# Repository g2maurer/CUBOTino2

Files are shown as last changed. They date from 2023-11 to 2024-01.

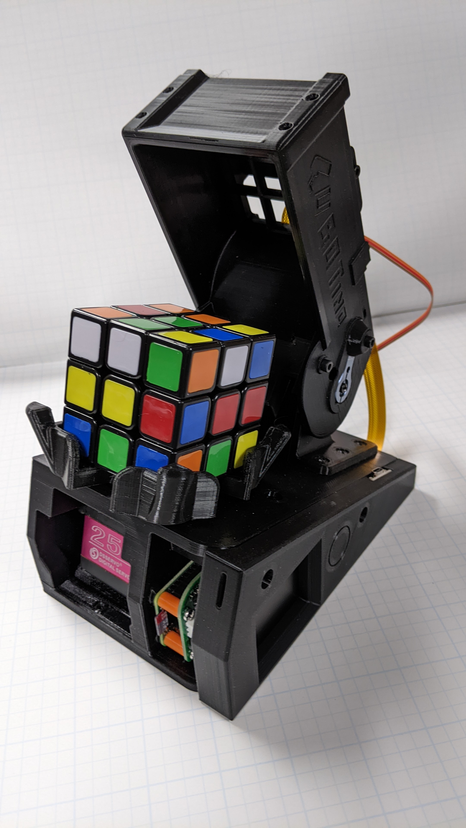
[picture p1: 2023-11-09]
Images/CUBOTino.jpg

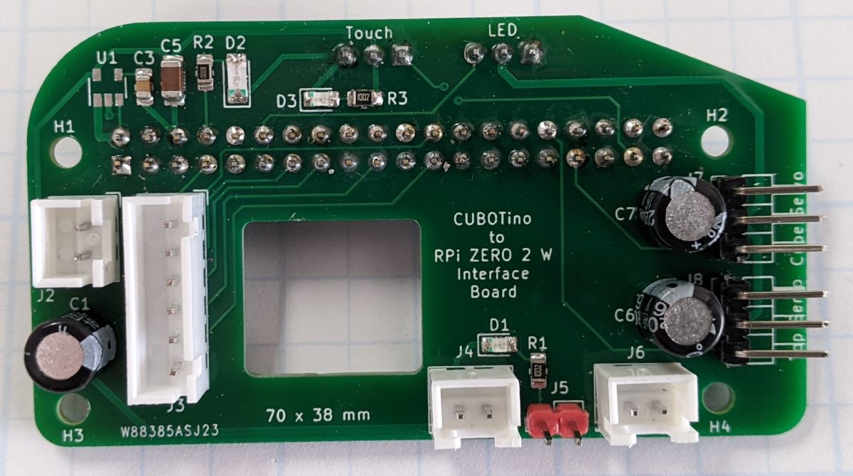
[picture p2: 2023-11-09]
Images/Cubotino_Interface_board_lr.jpg

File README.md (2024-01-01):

# CUBOTino2
 CUBOTino Modifications:
 1. No changes were made to software.
 2. Designed PCB (shield) to connect with RPi board.
 3. Modified cover STL file to be able to mount Display.
 4. Display is now cabled to PCB, not directly attached.
 5. Added photos in Images to help explain board connections and Display mounting.
 6. Photo DisplayMountScrews provides the part number for the screws used to mount the display. Screws were purchased from McMaster-Carr.
 7. The Bill of Materials (BOM) in found in the file PCB/CUBOTino2.csv
 8. The schematic is in the file PCB/CUBOTino2.pdf
 9. See file PCB/SMD Parts.txt for part sourcing info.

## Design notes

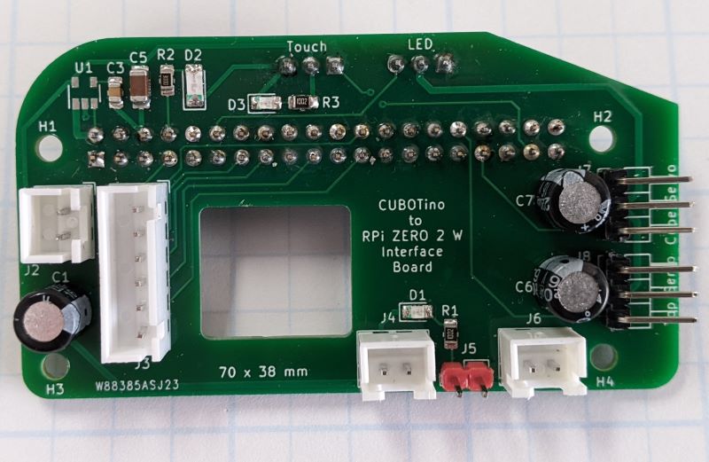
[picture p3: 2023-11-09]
Images/CUBOTino_5x7a.jpg

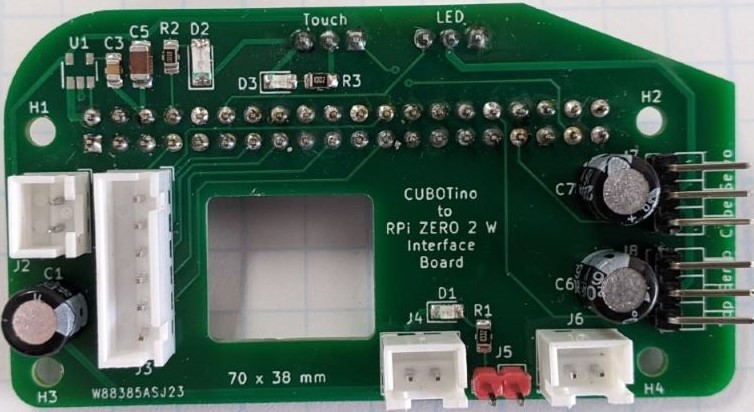
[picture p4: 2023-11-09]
Images/Cubotino_Interface_board_800.jpg

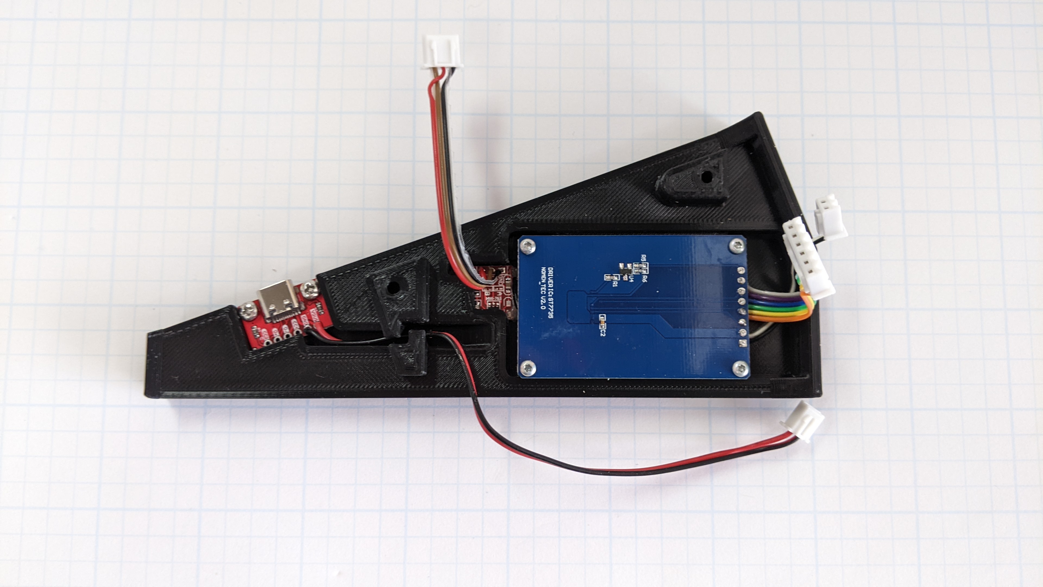
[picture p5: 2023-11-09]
Images/Display.jpg

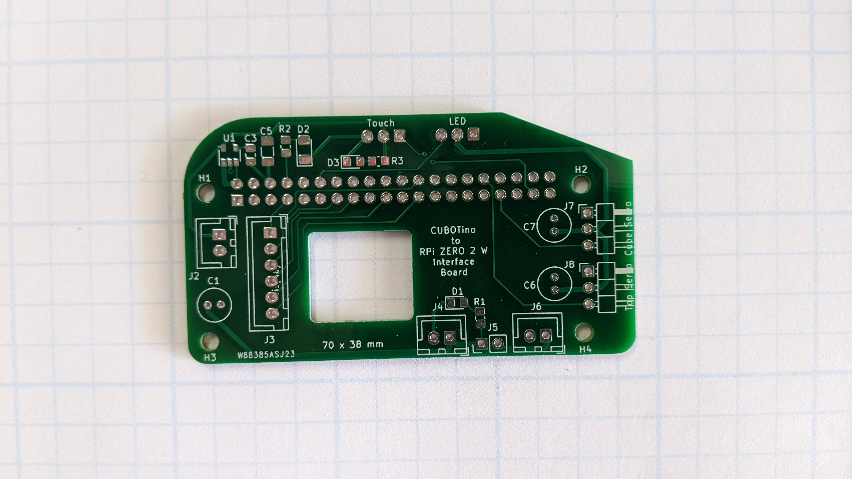
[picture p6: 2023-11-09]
Images/PCB.jpg

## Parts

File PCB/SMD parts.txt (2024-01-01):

I purchased the resistors, capacitors and LEDs on Amazon. They come as
> assorted kits. Here are some Amazon links to what I purchased:
>
> Resistors:
> https://www.amazon.com/gp/product/B09538ZBCR/ref=ppx_yo_dt_b_search_asin_title?ie=UTF8&th=1
> Capacitors:
> https://www.amazon.com/gp/product/B06XD3K15S/ref=ppx_yo_dt_b_search_asin_title?ie=UTF8&psc=1
> LEDs:
> https://www.amazon.com/gp/product/B01CUGA8JO/ref=ppx_yo_dt_b_search_asin_title?ie=UTF8&th=1
> Note: these are for is 0805 size components.
>
> The two components that are 1206 size are C5 and D2 (2.2uF capacitor and
> LED).
> Here is the links to the 1206 size components:
> LED:
> https://www.amazon.com/gp/product/B01CUGAFEC/ref=ppx_yo_dt_b_search_asin_title?ie=UTF8&th=1
> Capacitor:
> https://www.amazon.com/gp/product/B06XDHC93D/ref=ppx_yo_dt_b_search_asin_title?ie=UTF8&psc=1

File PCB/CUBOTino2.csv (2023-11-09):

Source: | C:\Users\gmaur\Documents\KiCad Projects\CUBOTino2\CUBOTino2.sch
Date: | 8/23/2023 4:29:55 PM
Tool: | Eeschema (5.1.10)-1
Component Count: | 28
Ref | Value | Footprint | Datasheet | Manufacturer | Vendor
C1 | 220uF 16V | Capacitor_THT:C_Radial_D5.0mm_H7.0mm_P2.00mm | ~
C2 | 100nF | Capacitor_SMD:C_0805_2012Metric_Pad1.18x1.45mm_HandSolder | ~
C3 | 10nF | Capacitor_SMD:C_0805_2012Metric_Pad1.18x1.45mm_HandSolder | ~
C4 | 100nF | Capacitor_SMD:C_0805_2012Metric_Pad1.18x1.45mm_HandSolder | ~
C5 | 2.2uF | Capacitor_SMD:C_1206_3216Metric_Pad1.33x1.80mm_HandSolder | ~
C6 | 220uF 16V | Capacitor_THT:C_Radial_D5.0mm_H7.0mm_P2.00mm | ~
C7 | 220uF 16V | Capacitor_THT:C_Radial_D5.0mm_H7.0mm_P2.00mm | ~
D1 | LED | LED_SMD:LED_0805_2012Metric_Pad1.15x1.40mm_HandSolder | ~
D2 | LED | LED_SMD:LED_1206_3216Metric_Pad1.42x1.75mm_HandSolder | ~
D3 | LED | LED_SMD:LED_0805_2012Metric_Pad1.15x1.40mm_HandSolder | ~
H1 | MountingHole | MountingHole:MountingHole_2.7mm | ~
H2 | MountingHole | MountingHole:MountingHole_2.7mm | ~
H3 | MountingHole | MountingHole:MountingHole_2.7mm | ~
H4 | MountingHole | MountingHole:MountingHole_2.7mm | ~
J1 | P1 | Connector_PinSocket_2.54mm:PinSocket_2x20_P2.54mm_Vertical | https://www.raspberrypi.org/documentation/hardware/raspberrypi/schematics/rpi_SCH_3bplus_1p0_reduced.pdf
J2 | TFT_PWR | Connector_JST:JST_XH_B2B-XH-A_1x02_P2.50mm_Vertical | ~
J3 | TFT | Connector_JST:JST_XH_B6B-XH-A_1x06_P2.50mm_Vertical | ~
J4 | 5V | Connector_JST:JST_XH_B2B-XH-A_1x02_P2.50mm_Vertical | ~
J5 | Jump | Connector_PinHeader_2.54mm:PinHeader_1x02_P2.54mm_Vertical | ~
J6 | 5VP | Connector_JST:JST_XH_B2B-XH-A_1x02_P2.50mm_Vertical | ~
J7 | Cube | Connector_PinHeader_2.54mm:PinHeader_1x03_P2.54mm_Horizontal | ~
J8 | Top | Connector_PinHeader_2.54mm:PinHeader_1x03_P2.54mm_Horizontal | ~
J9 | LED | Connector_JST:JST_XH_B3B-XH-A_1x03_P2.50mm_Vertical | ~
J10 | Touch | Connector_JST:JST_XH_B3B-XH-A_1x03_P2.50mm_Vertical | ~
R1 | 10k | Resistor_SMD:R_0805_2012Metric_Pad1.20x1.40mm_HandSolder | ~
R2 | 330 | Resistor_SMD:R_0805_2012Metric_Pad1.20x1.40mm_HandSolder | ~
R3 | 10k | Resistor_SMD:R_0805_2012Metric_Pad1.20x1.40mm_HandSolder | ~
U1 | LP2985-3.3 | Package_TO_SOT_SMD:SOT-23-5 | http://www.ti.com/lit/ds/symlink/lp2985.pdf

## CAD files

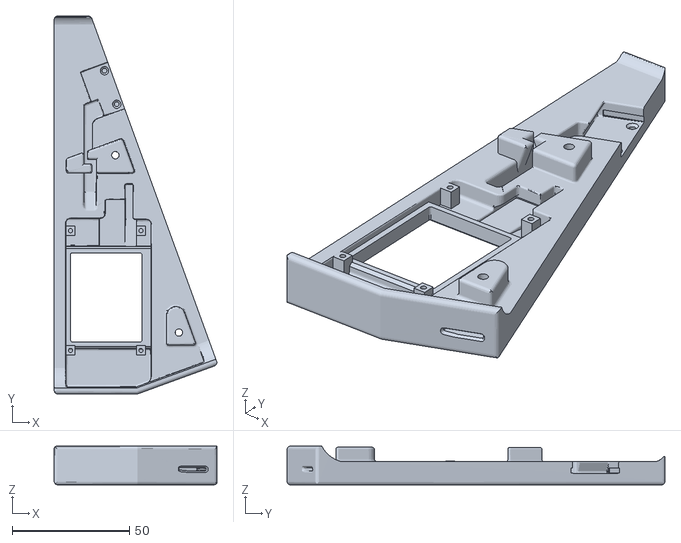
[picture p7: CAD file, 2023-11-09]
STL/PCB_Cover6.stl
69.3 x 161.0 x 16.5

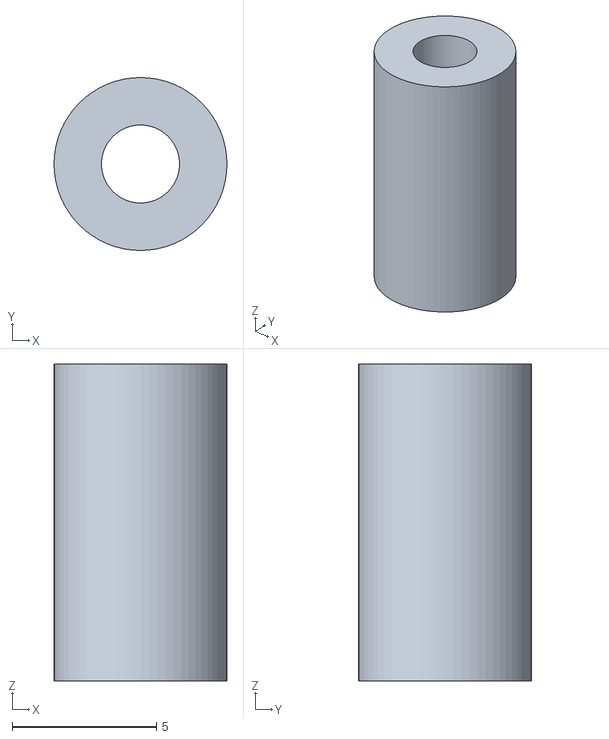
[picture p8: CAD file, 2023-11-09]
STL/Spacer_6x11mm.stl
6.00 x 6.00 x 11.0

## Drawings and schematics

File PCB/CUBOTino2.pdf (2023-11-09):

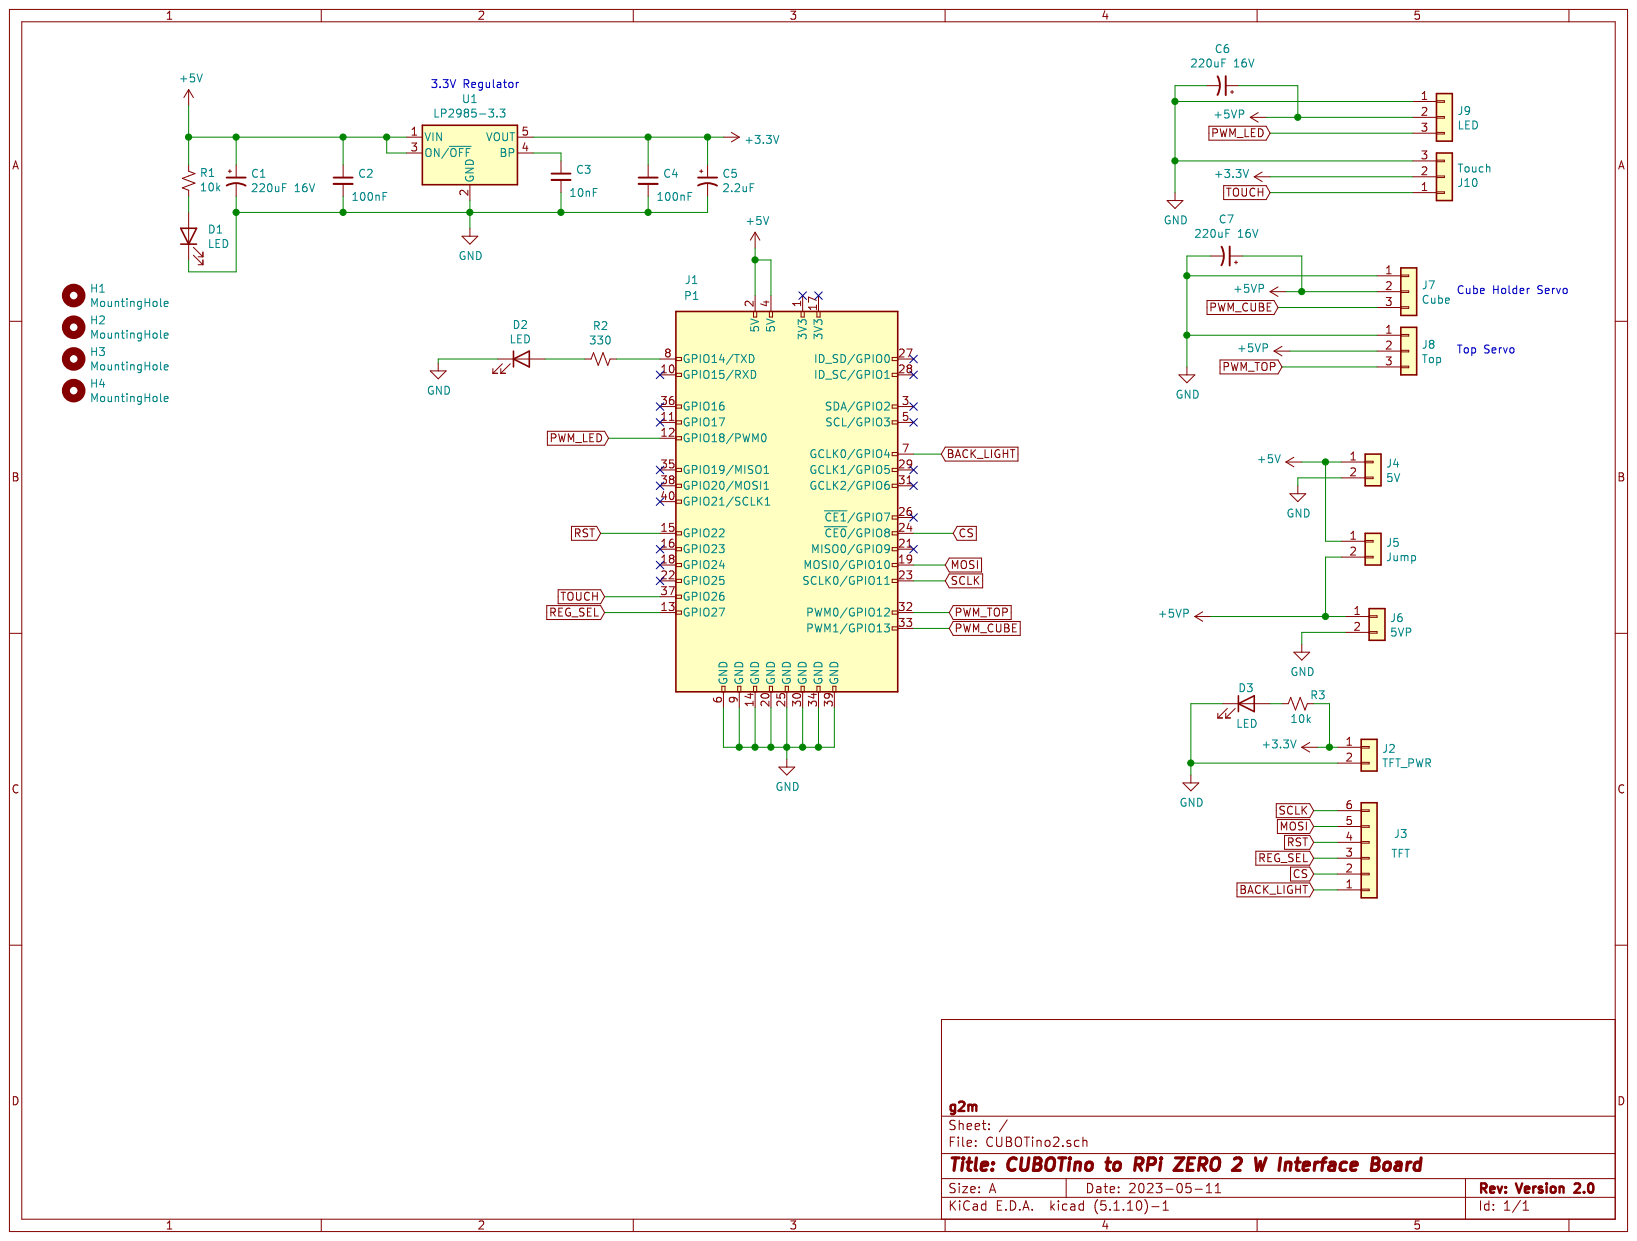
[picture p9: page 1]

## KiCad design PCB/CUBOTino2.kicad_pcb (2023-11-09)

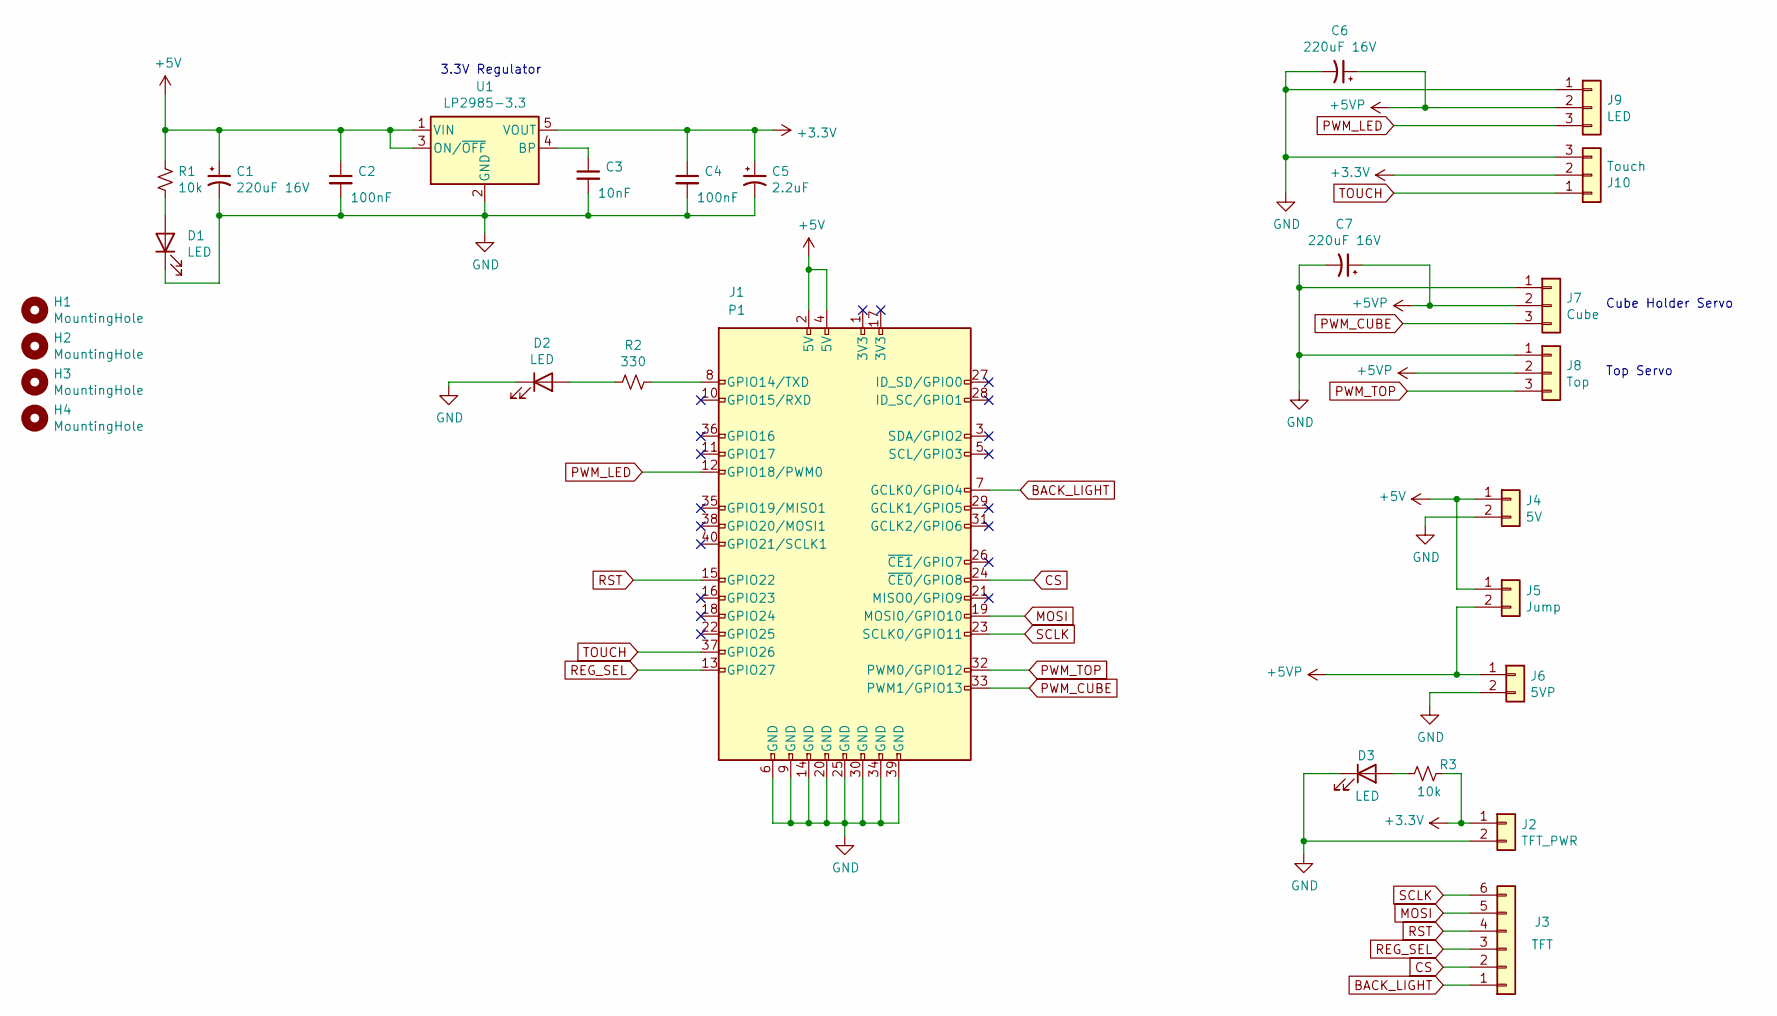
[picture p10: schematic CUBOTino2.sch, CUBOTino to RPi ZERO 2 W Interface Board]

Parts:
C1, C6, C7: 220uF 16V; C_Radial_D5.0mm_H7.0mm_P2.00mm
C2, C4: 100nF; C_0805_2012Metric_Pad1.18x1.45mm_HandSolder
C3: 10nF; C_0805_2012Metric_Pad1.18x1.45mm_HandSolder
C5: 2.2uF; C_1206_3216Metric_Pad1.33x1.80mm_HandSolder
D1, D3: LED; LED_0805_2012Metric_Pad1.15x1.40mm_HandSolder
D2: LED; LED_1206_3216Metric_Pad1.42x1.75mm_HandSolder
H1, H2, H3, H4: MountingHole; MountingHole_2.7mm
J1: P1; PinSocket_2x20_P2.54mm_Vertical
J2: TFT_PWR; JST_XH_B2B-XH-A_1x02_P2.50mm_Vertical
J3: TFT; JST_XH_B6B-XH-A_1x06_P2.50mm_Vertical
J4: 5V; JST_XH_B2B-XH-A_1x02_P2.50mm_Vertical
J5: Jump; PinHeader_1x02_P2.54mm_Vertical
J6: 5VP; JST_XH_B2B-XH-A_1x02_P2.50mm_Vertical
J7: Cube; PinHeader_1x03_P2.54mm_Horizontal
J8: Top; PinHeader_1x03_P2.54mm_Horizontal
J9: LED; JST_XH_B3B-XH-A_1x03_P2.50mm_Vertical
J10: Touch; JST_XH_B3B-XH-A_1x03_P2.50mm_Vertical
R1, R3: 10k; R_0805_2012Metric_Pad1.20x1.40mm_HandSolder
R2: 330; R_0805_2012Metric_Pad1.20x1.40mm_HandSolder
U1: LP2985-3.3; SOT-23-5

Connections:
+3V3: C4.1, C5.1, J2.1, J10.2, R3.2, U1.5 (VOUT)
+5V: C1.1, C2.1, J1.2 (5V), J1.4 (5V), J4.1, J5.1, R1.2, U1.1 (VIN), U1.3 (ON/~OFF~)
+5VP: C6.1, C7.1, J5.2, J6.1, J7.2, J8.2, J9.2
BACK_LIGHT: J1.7 (GCLK0/GPIO4), J3.1
CS: J1.24 (~CE0~/GPIO8), J3.2
GND: C1.2, C2.2, C3.2, C4.2, C5.2, C6.2, C7.2, D1.1 (K), D2.1 (K), D3.1 (K), J1.6 (GND), J1.9 (GND), J1.14 (GND), J1.20 (GND), J1.25 (GND), J1.30 (GND), J1.34 (GND), J1.39 (GND), J2.2, J4.2, J6.2, J7.1, J8.1, J9.1, J10.3, U1.2 (GND)
MOSI: J1.19 (MOSI0/GPIO10), J3.5
unnamed: C3.1, U1.4 (BP)
unnamed: D1.2 (A), R1.1
unnamed: D2.2 (A), R2.1
unnamed: D3.2 (A), R3.1
unnamed: J1.8 (GPIO14/TXD), R2.2
PWM_CUBE: J1.33 (PWM1/GPIO13), J7.3
PWM_LED: J1.12 (GPIO18/PWM0), J9.3
PWM_TOP: J1.32 (PWM0/GPIO12), J8.3
REG_SEL: J1.13 (GPIO27), J3.3
RST: J1.15 (GPIO22), J3.4
SCLK: J1.23 (SCLK0/GPIO11), J3.6
TOUCH: J1.37 (GPIO26), J10.1

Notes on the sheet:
Cube Holder Servo
Top Servo
3.3V Regulator

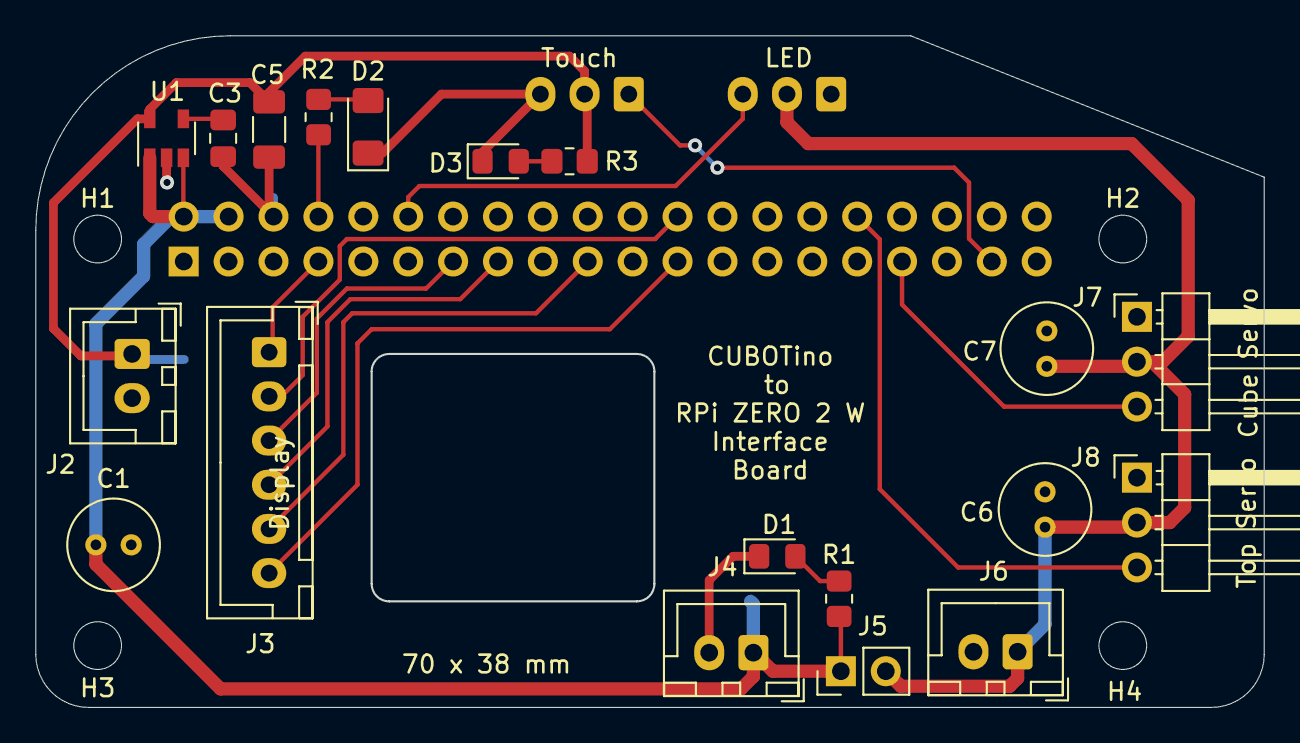
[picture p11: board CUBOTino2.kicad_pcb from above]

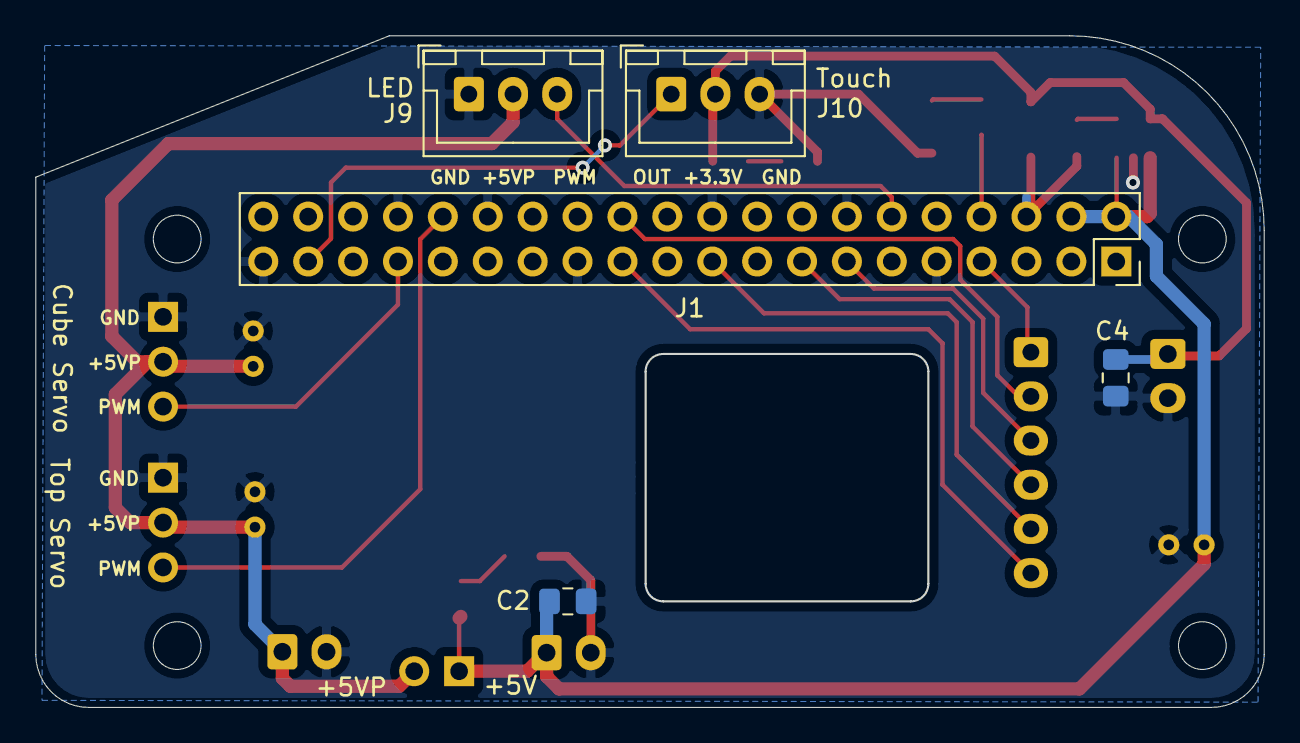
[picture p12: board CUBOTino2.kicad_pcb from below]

Board: 2 copper layers, 69.5 x 38.0 mm, 28 parts (5 on the bottom side), 19 nets.

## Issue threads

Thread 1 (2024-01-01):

SMD's

daincrawford, 2024-01-01:
I there any chance we could get a list of the LEDs, resistors and small surface mount capacitors. Adafruit has the large capacitors, but none of the surface mount. I have looked at DigiKey and Mouser, but I have no idea what I actually need. I was able to get your boards from PCBway. Thank you very much for making them available and I am really looking forward to completing this project.
I have all of the rest of the parts either ordered or already received.  Again thank you for your fine work.

g2maurer, 2024-01-01:
I will send you a list.

On Mon, Jan 1, 2024 at 6:04 AM daincrawford ***@***.***>
wrote:

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

g2maurer, 2024-01-01:
I purchased the resistors, capacitors and LEDs on Amazon. They come as assorted kits. Here are some Amazon links to what I purchased:

Resistors:  https://www.amazon.com/gp/product/B09538ZBCR/ref=ppx_yo_dt_b_search_asin_title?ie=UTF8&th=1
Capacitors:  https://www.amazon.com/gp/product/B06XD3K15S/ref=ppx_yo_dt_b_search_asin_title?ie=UTF8&psc=1
LEDs:  https://www.amazon.com/gp/product/B01CUGA8JO/ref=ppx_yo_dt_b_search_asin_title?ie=UTF8&th=1
Note: these are for is 0805 size components.

The two components that are 1206 size are C5 and D2 (2.2uF capacitor and LED).
Here is the links to the 1206 size components:
LED:  https://www.amazon.com/gp/product/B01CUGAFEC/ref=ppx_yo_dt_b_search_asin_title?ie=UTF8&th=1
Capacitor:  https://www.amazon.com/gp/product/B06XDHC93D/ref=ppx_yo_dt_b_search_asin_title?ie=UTF8&psc=1

I have in the past put the 0805 components on the 1206 pads.

I have purchased individual components from Mouser but I found it cheaper to just buy the kits from Amazon.
The individual components are typically cheaper from Mouser but the shipping results in them being just as costly as Amazon.

g2maurer, 2024-01-01:
BTW: The BOM is in the file PCB/CUBOTino2.csv

daincrawford, 2024-01-01:
Gerald,
Thank you so much for the quick thorough response. My order is already
placed.
These were the last parts that I needed tied down.
I will let you know how this project turns out.
Dain

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

g2maurer, 2024-02-12:
I purchased the surface mount components on Amazon. The SMD sizes I used
are 0805 and 1206.
The BOM lists the size of each component.
Here are some links to the parts I purchased on Amazon.

https://www.amazon.com/gp/product/B06XD3K15S/ref=ppx_yo_dt_b_search_asin_title?ie=UTF8&psc=1
     Capacitors  size  0805

https://www.amazon.com/gp/product/B06XDHC93D/ref=ppx_yo_dt_b_search_asin_title?ie=UTF8&psc=1
    Capacitors size 1206

https://www.amazon.com/gp/product/B09538ZBCR/ref=ppx_yo_dt_b_search_asin_title?ie=UTF8&th=1
      Resistors size 0805

https://www.amazon.com/gp/product/B01CUGA8JO/ref=ppx_yo_dt_b_search_asin_title?ie=UTF8&th=1
     LEDs size 0805

https://www.amazon.com/gp/product/B01CUGAFEC/ref=ppx_yo_dt_b_search_asin_title?ie=UTF8&th=1
     LEDs  size 1206

On Mon, Jan 1, 2024 at 6:04 AM daincrawford ***@***.***>
wrote:

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

Closed 2024-02-10.

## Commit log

2023-11-09 CUBOTino modifications
    Modifications:
    [CUBOTino2-B_Cu.gbr, CUBOTino2-B_Mask.gbr, CUBOTino2-B_Paste.gbr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]
2023-11-09 Adding STL files
    Added files that were modified to use PCB design.
    [PCB_Cover6.stl, Spacer_6x11mm.stl]
2023-11-09 Added Photos
    Added photos to help explain the board connections and display mounting.
2023-11-09 Added additional Photos
    Added PCB Photos
2024-01-01 Create SMD parts.txt
    Added file to help with acquiring surface mount parts.
